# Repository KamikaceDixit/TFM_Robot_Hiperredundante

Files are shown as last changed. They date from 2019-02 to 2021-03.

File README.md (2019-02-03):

# MACH I. Un manipulador actuado por cables hiperredundante
MACH I es el resultado de un proyecto de fin de máster realizado en la Escuela Superior de Ingenieros Industriales de la UPM. El objetivo de dicho proyecto era construir un robot hiperredundante funcional, que pudiera ser utilizado en un futuro para probar nuevos algoritmos de movimiento en este tipo de robots. El resultado del proyecto es el siguiente.

<div>
<a href="../../tree/master/Renders">
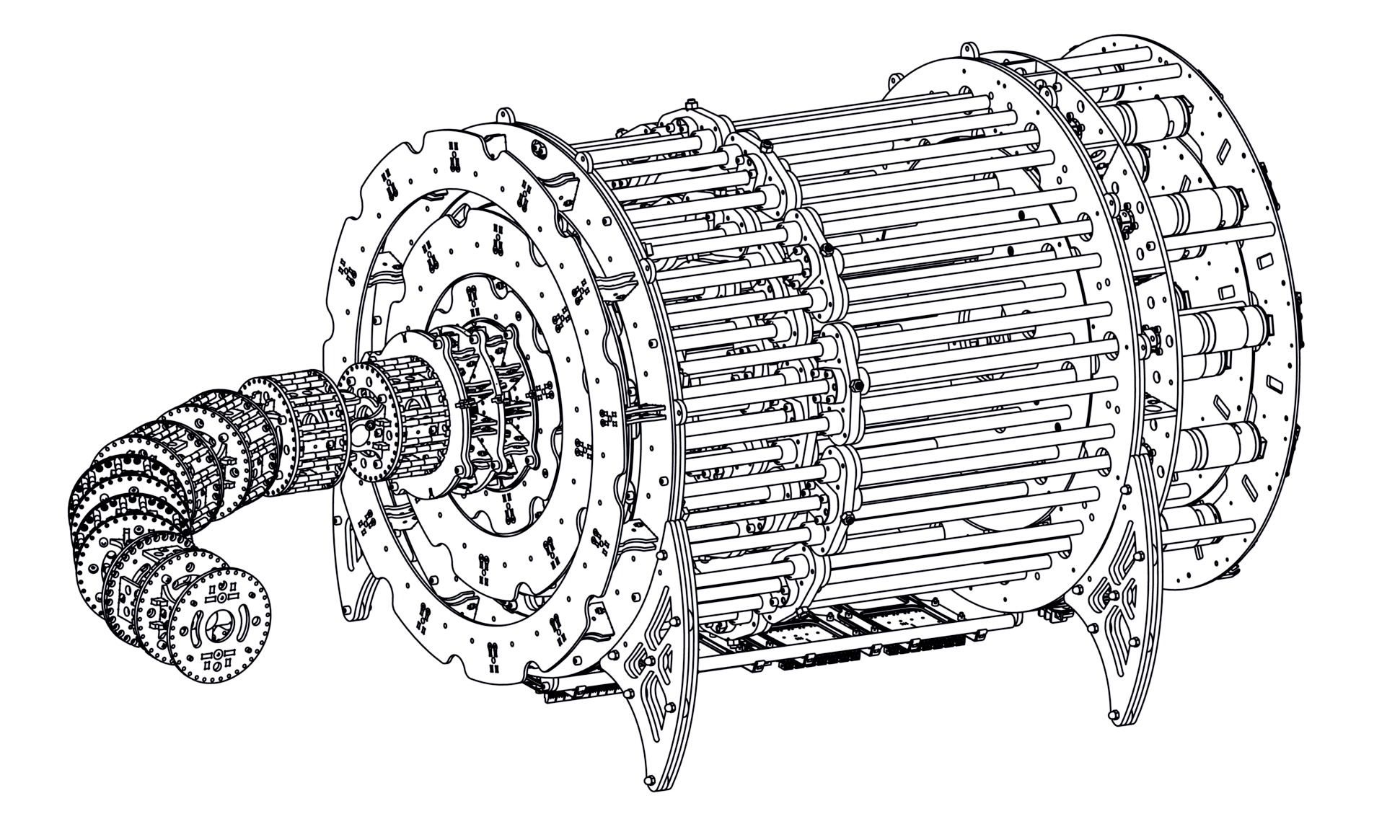
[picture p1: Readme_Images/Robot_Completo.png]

</a>
</div>

Se trata de un robot hiperredundante con 17 grados de libertad. Se compone de 7 rótulas con 2 grados de libertad cada una una, más 3 gdl extra para poder accionar una pinza o cualquier otro elemento en el extremo.
Cada rótula esta controlada con 3 cables equidistantes 120º y el rango de giro de cada una es de 33º con respecto a cualquier eje contenido en el plano paralelo a la base fija de la rótula que pase por el centro de la misma.

La concepción de MACH I se divide en 3 partes:
- Parte mecánica
- Parte electrónica y eléctrica
- Parte de programación
<hr />
En el repositorio, el proyecto esta descompuesto en varias carpetas.

### CAD y Planos
En dicha carpeta se encuentran todos los archivos CAD pertenecientes la proyecto. Estan desarrollados en CATIA V5 R21.
### Control Dinámico
Se recogen los ficheros de Matlab y diversas pruebas realizadas para caracterizar el conjunto "control+motor" para poder ajustar los diferentes parametros del control. En él se encuentran diversos archivos de Matlab y Simulink.
### PCBs
Se encuentran todos los ficheros utilizados para realizar las placas de electrónica, incluyendo esquemáticos, pcbs y librerías.
### Programas
Aquí estan desarrollados los programas integrados en cada placa y la Interfaz Hombre Máquina desarrollada en Matlab.
### Renders
Carpeta que recoge varios Renders realizados a partir del CAD.
<hr />

Adicionalmente, se recoge diverso material gráfico del proyecto en Flickr y YouTube, y puede ser consultado en los siguiente enlaces:
<div align="center">
<a href="https://www.flickr.com/photos/156143787@N03/collections/72157706450447504/">
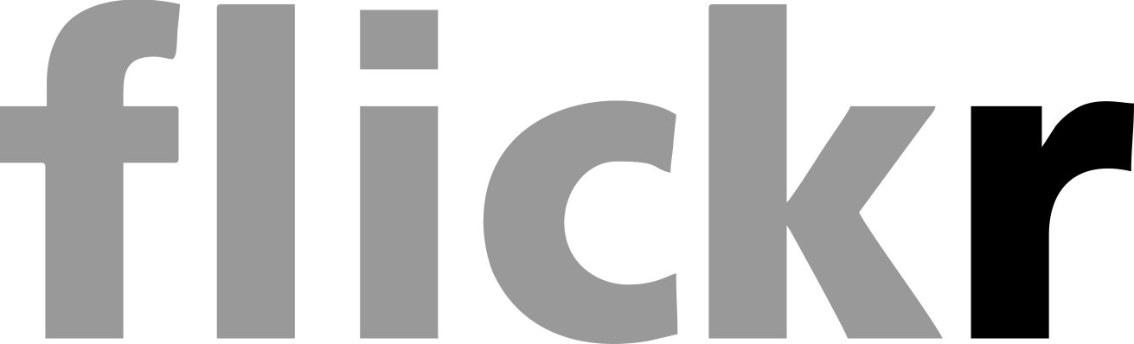
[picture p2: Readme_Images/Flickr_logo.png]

</a>
<a href="https://www.youtube.com/playlist?list=PLwVt_GYxzsi9YXO1_7UndzVlK2NOCYKW8">
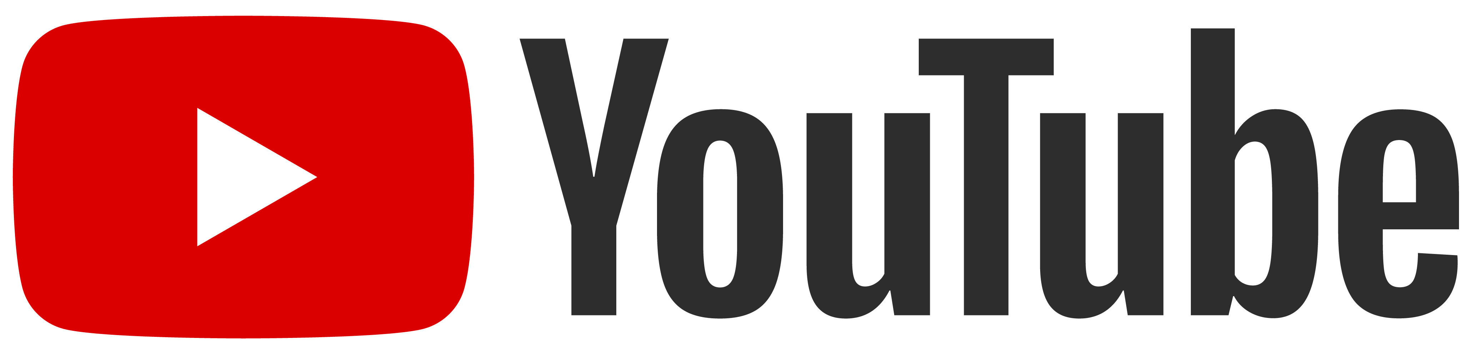
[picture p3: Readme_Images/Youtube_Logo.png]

</a>
</div>

<hr />

<a data-flickr-embed="true" data-footer="true" data-context="true"  href="https://www.flickr.com/photos/156143787@N03/46243925134/" title="Robot_3">Robot_3</a>

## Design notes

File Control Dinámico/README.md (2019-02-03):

# Control dínamico Motores
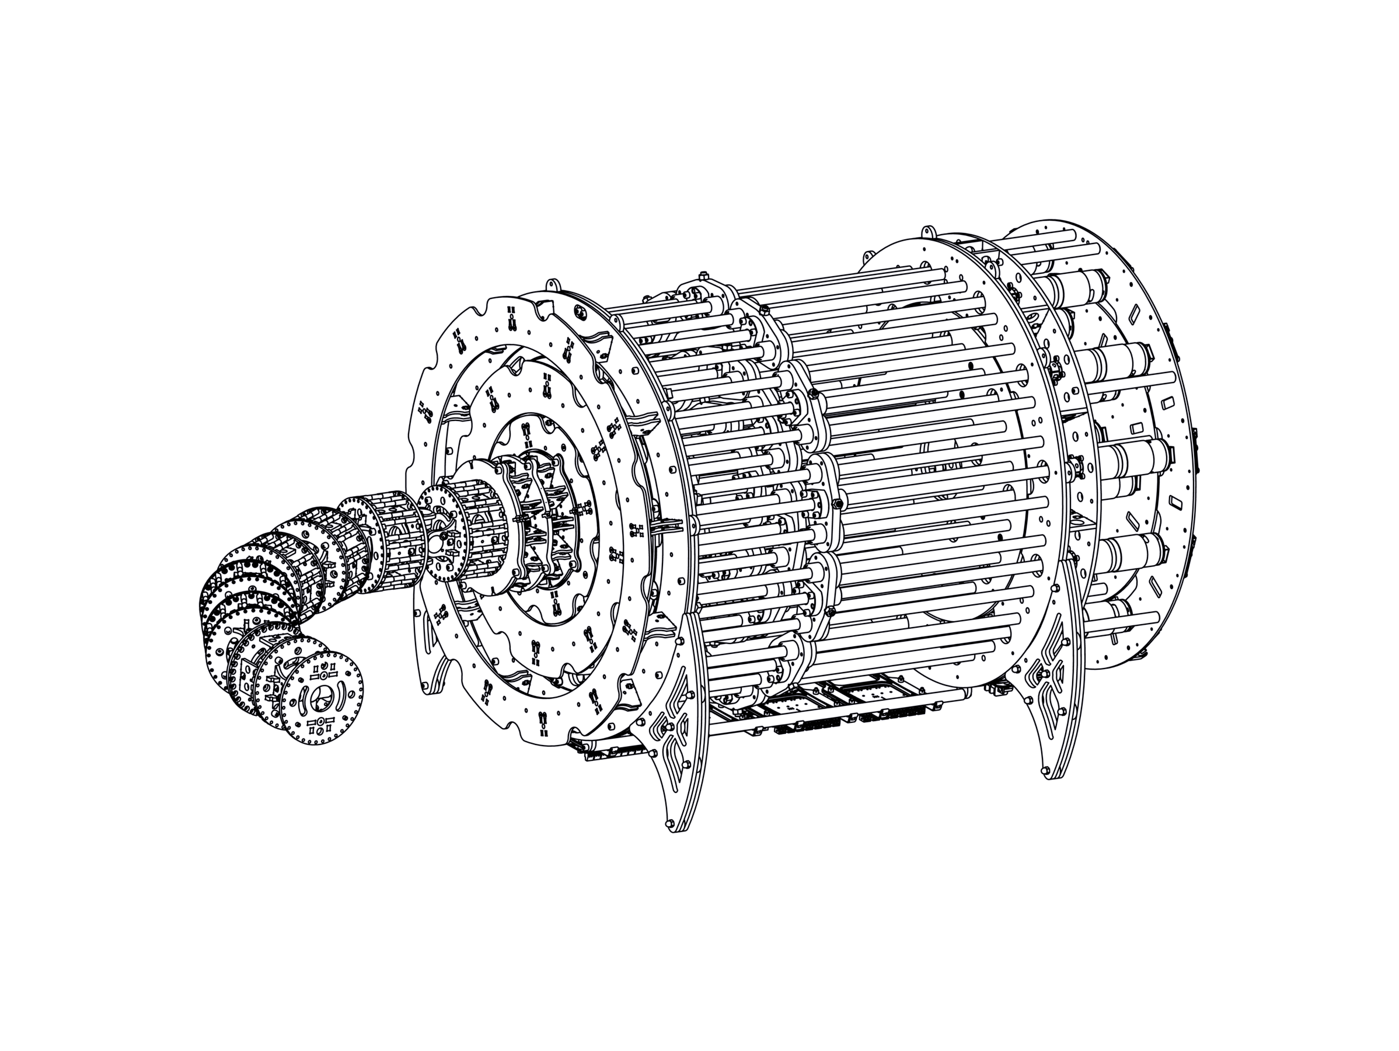
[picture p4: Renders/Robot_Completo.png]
N|Solid


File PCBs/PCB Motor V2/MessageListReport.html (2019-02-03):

Altium customize

# Message List

Date: | | 11/06/2018
Time: | | 3:35:03
Elapsed Time: | | 00:00:00

Class | Document | Source | Message | Time | Date | No.
Situs Event | Placa_Sencilla_v2.PcbDoc | Situs | Routing Started | 3:31:26 | 11/06/2018 | 1
Routing Status | Placa_Sencilla_v2.PcbDoc | Situs | Creating topology map | 3:31:26 | 11/06/2018 | 2
Situs Event | Placa_Sencilla_v2.PcbDoc | Situs | Starting Fan out to Plane | 3:31:26 | 11/06/2018 | 3
Situs Event | Placa_Sencilla_v2.PcbDoc | Situs | Completed Fan out to Plane in 0 Seconds | 3:31:26 | 11/06/2018 | 4
Situs Event | Placa_Sencilla_v2.PcbDoc | Situs | Starting Memory | 3:31:26 | 11/06/2018 | 5
Situs Event | Placa_Sencilla_v2.PcbDoc | Situs | Completed Memory in 0 Seconds | 3:31:27 | 11/06/2018 | 6
Situs Event | Placa_Sencilla_v2.PcbDoc | Situs | Starting Layer Patterns | 3:31:27 | 11/06/2018 | 7
Routing Status | Placa_Sencilla_v2.PcbDoc | Situs | 78 of 161 connections routed (48,45%) in 3 Seconds | 3:31:29 | 11/06/2018 | 8
Situs Event | Placa_Sencilla_v2.PcbDoc | Situs | Completed Layer Patterns in 3 Seconds | 3:31:30 | 11/06/2018 | 9
Situs Event | Placa_Sencilla_v2.PcbDoc | Situs | Starting Multilayer Main | 3:31:30 | 11/06/2018 | 10
Routing Status | Placa_Sencilla_v2.PcbDoc | Situs | 159 of 161 connections routed (98,76%) in 2 Minutes 58 Seconds | 3:34:24 | 11/06/2018 | 11
Situs Event | Placa_Sencilla_v2.PcbDoc | Situs | Completed Multilayer Main in 2 Minutes 54 Seconds | 3:34:25 | 11/06/2018 | 12
Situs Event | Placa_Sencilla_v2.PcbDoc | Situs | Starting Completion | 3:34:25 | 11/06/2018 | 13
Routing Status | Placa_Sencilla_v2.PcbDoc | Situs | 160 of 161 connections routed (99,38%) in 3 Minutes 7 Seconds | 3:34:33 | 11/06/2018 | 14
Situs Event | Placa_Sencilla_v2.PcbDoc | Situs | Completed Completion in 8 Seconds | 3:34:33 | 11/06/2018 | 15
Situs Event | Placa_Sencilla_v2.PcbDoc | Situs | Starting Spread | 3:34:33 | 11/06/2018 | 16
Routing Status | Placa_Sencilla_v2.PcbDoc | Situs | 160 of 161 connections routed (99,38%) in 3 Minutes 13 Seconds | 3:34:39 | 11/06/2018 | 17
Situs Event | Placa_Sencilla_v2.PcbDoc | Situs | Completed Spread in 6 Seconds | 3:34:40 | 11/06/2018 | 18
Situs Event | Placa_Sencilla_v2.PcbDoc | Situs | Starting Straighten | 3:34:40 | 11/06/2018 | 19
Routing Status | Placa_Sencilla_v2.PcbDoc | Situs | 160 of 161 connections routed (99,38%) in 3 Minutes 17 Seconds | 3:34:43 | 11/06/2018 | 20
Situs Event | Placa_Sencilla_v2.PcbDoc | Situs | Completed Straighten in 4 Seconds | 3:34:44 | 11/06/2018 | 21
Routing Status | Placa_Sencilla_v2.PcbDoc | Situs | 160 of 161 connections routed (99,38%) in 3 Minutes 18 Seconds | 3:34:44 | 11/06/2018 | 22
Situs Event | Placa_Sencilla_v2.PcbDoc | Situs | Routing finished with 0 contentions(s). Failed to complete 1 connection(s) in 3 Minutes 18 Seconds | 3:34:44 | 11/06/2018 | 23

Back to top

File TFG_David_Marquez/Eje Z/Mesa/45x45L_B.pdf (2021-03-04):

# Profile 45x45L B-Type slot 10

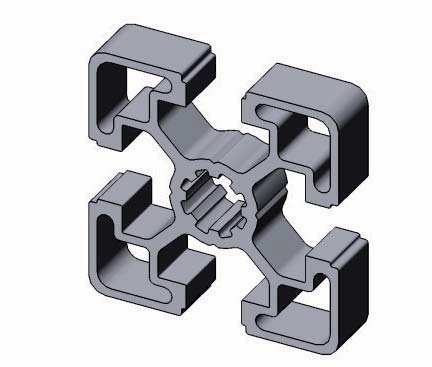
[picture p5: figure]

Profile 45x45L B-Type slot 10

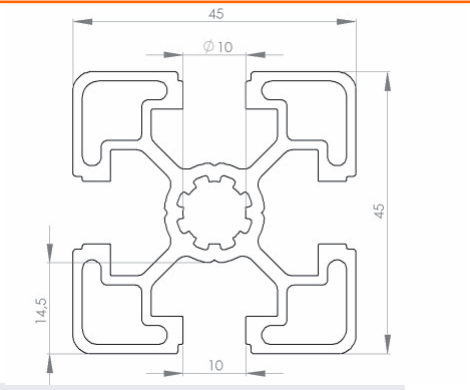
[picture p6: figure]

Slot | | 10 | mm
Mass | m | 1,50 | Kg/m
Moment of Inertia | Ix | 11,00 | cm⁴
| Iy | 11,00 | cm⁴
Section modulus | Wx | 4,80 | cm³
| Wy | 4,80 | cm³
Surface | A | 5,70 | cm²

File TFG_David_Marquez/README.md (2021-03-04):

# Control y Teleoperación de Mach I, un robot manipulador híper redundante para tareas de inspección
Trabajo de Fin de Grado de David Márquez Alcolea para la obtención del Grado en Ingeniería en Tecnologías Industriales de la ETSII - UPM.

<hr />
En el repositorio, el proyecto está descompuesto en varias carpetas.

### Eje Z
Compone los ensamblajes y piezas diseñadas para el mecanismo de movimiento lineal del eje Z del robot Mach I.
### PCB_Emergencia
Compone todos los archivos de diseño, datasheets, código y librerías de la placa electrónica para casos de emergencia diseñada para el robot.
### Unity
Se encuentran los proyectos del simulador creado en el motor gráfico Unity3D. Se debe remarcar que GitHub no permite subir archivos de más de 100mb, por lo que hay archivos críticos que no han podido subirse a este repositorio, como los modelos 3D del robot. Contactar con el creador para recibir estos archivos.

<hr />

Adicionalmente, se recoge diverso material gráfico del proyecto en Flickr y YouTube, y puede ser consultado en los siguiente enlaces:
<div align="center">
<a href="https://flic.kr/s/aHsmUDHa3X">

</a>
<a href="https://www.youtube.com/watch?v=YmS-nTq0sPs&list=PL655qwW_R3OX9st5jwc-Hn8Ow5uMBquOL">

</a>
</div>

<hr />

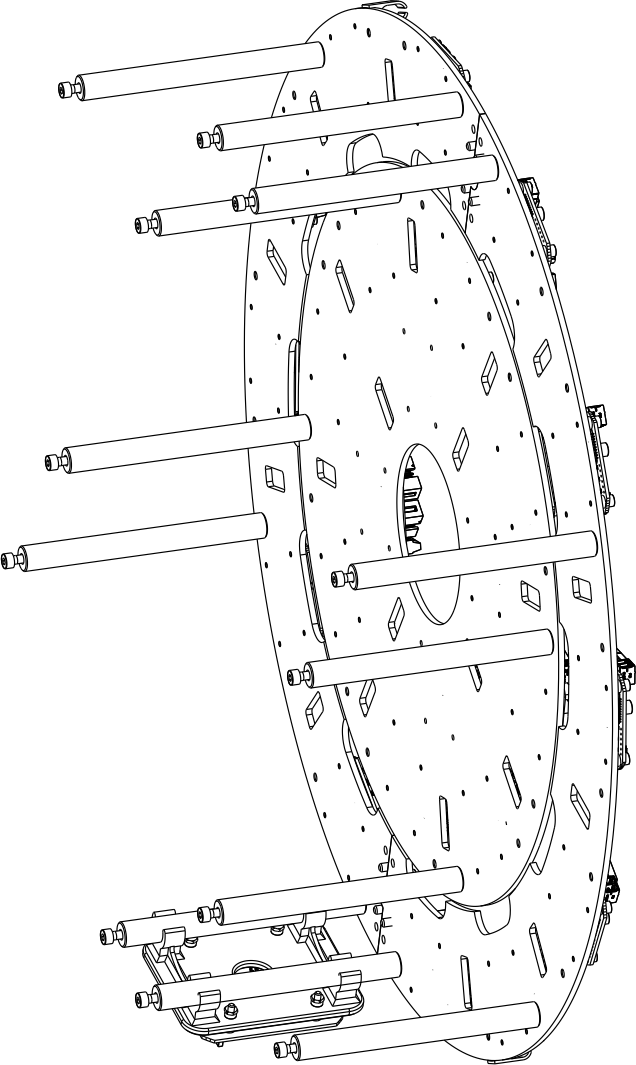
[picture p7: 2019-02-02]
Renders/Placa_Electronica.png

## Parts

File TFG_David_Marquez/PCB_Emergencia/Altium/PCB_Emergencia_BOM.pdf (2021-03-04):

Bill of Materials | Bill of Materials for PCB Emergencia
Source Data From: | BOM.BomDoc
Project: | PCB_Emergencia.PrjPcb
Variant: | 1,0
Designator | Name | LibRef | Footprint | Description | Quantity
C1, C2, C3, C4, C5, C6, C7, C8, C9, C10, C11, C12, C15, C16, C17, C18, C19, C21, C22, C23
Capacitors. | CAP0805 | 0805 | 20
C13, C14 | 47u | 47UF-50V-20% | PANASONIC_D | 2
C20 | 4.7u | 47UF-50V-20% | PANASONIC_D | 1
D1, D4, D6 | SS26FL | SS26FL | SS26FL | 3
D2 | LED Encendido | LED1206 | LED-1206 | 1
D3 | LED Parada | LED1206 | LED-1206 | 1
D5 | 13V Zener MM1Z13 | DIODE-ZENER16V | SOD-123 | 1
D7 | LED Standby | LED1206 | LED-1206 | 1
D8 | LED Carga | LED1206 | LED-1206 | 1
IC1 | TP4056 | TP4056 | *SOP-8 | 1
JP1, JP2 | JUMPER-PAD-2- NC_BY_PASTE | JUMPER-PAD-2- NC_BY_PASTE | PAD-JUMPER-2- NC_BY_PASTE_YES_SILK | 2
L1 | CDRH74 | CDRH74 | CDRH74 | 1
L2 | SMMS1360 | INDUCTOR | SMMS1360 | 1
Q1 | IRF7832TRPBF | N-MOSFET-SO8S | SO-08 | 1
R1, R2, R3, R4, R5, R6, R7, R8, R9, R10, R11, R14, R15, R16, R18, R19, R20 | Resistors. | RESISTOR0805-RES | 0805 | 17
R12 | 20K | RESISTOR0805-RES | 0805 | | 1
R13, R17 | 3296W | 3296W | 3296W | | 2
U2 | NCP1117 | V_REG_LM1117SOT223 | SOT223 | | 1
U1 | ATmega328-AU | ATmega328-AU | 32A_N | 8-bit AVR Microcontroller, 32KB Flash, 1KB EEPROM, 2KB SRAM, 32-pin TQFP, Industrial Grade (-40°C to 85°C) | 1
Y1, Y2 | 16MHz | NX3225SA-16.000MHZ-STD- CSR-1 | NDK NX3225SA | CRYSTAL 16.0000MHZ 8PF SMD | 2
E_C1, E_C2 | Header 2 | Header 2 | HDR1X2 | Header, 2-Pin | 2
P1 | IDC2X4 | IDC2X4 | IDC2X4 | Header, 4-Pin, Dual row | 1
Prog1 | Header 6 | Header 6 | HDR1X6 | Header, 6-Pin | 1
U4 | MT3608 | MT3608 | *SOT23-6 | High Efficiency 1.2MHz 2A Step Up Converter | 1
MCP2 | MCP2551T-I/SN | MCP2551T-I/SN | SOIC-SN8_N | High-Speed CAN Transceiver, 8-Pin SOIC, Industrial Temperature, Tape and Reel | 1
J1 | Conector JST | S2B-PH-K-S(LF)(SN) | *JST_S2B-PH-K-S(LF)(SN) | PH Series 2 Position 2.0 mm Through Hole Side Entry Shrouded Header | 1
U3 | LM2596S | LM2596S | LM2596S | Semiconductors and Actives | 1
MCP1 | MCP2515T-I/SO | MCP2515T-I/SO | SOIC-SO18_N | Stand-Alone CAN Controller With SPI Interface, 18-Pin SOIC, Industrial | 1
S1 | FSMSMTR | FSMSMTR | TE FSMSMTR | SWITCH TACTILE SPST-NO 0.05A 24V | 1
J2 | 20020110-D021A01LF | 20020110-D021A01LF | FCI 06-381-2PIN | TERM BLOCK HDR 2POS R/A 3.81MM | 1
| | | | | 72
Altium Limited Confidential | 29/11/2020 | Page 1

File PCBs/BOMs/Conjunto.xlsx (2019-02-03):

Bill of Materials
Source Data From: |  | Placas_PCB
Project: |  | Robot_Hiperredundante
Variant:
Creation Date: | 13/06/2018 | 1:45:41
Print Date: | 2018-07-05 | 16:44:05
Footprint | Comment | Link | Designator | Description | Quantity | A pedir | Control | Alimentacion | Fdc | Motores | 9V
0805 | 100n | https://lcsc.com/product-detail/Multilayer-Ceramic-Capacitors-MLCC-SMD-SMT_100nF-104-10-50V_C38141.html |  |  | 224 | 250 | 7 | 42 | 7 | 168
0805 | 22p | https://lcsc.com/product-detail/Multilayer-Ceramic-Capacitors-MLCC-SMD-SMT_22pF-220-5-50V_C105623.html |  |  | 137 | 200 | 2 | 10 | 5 | 120
0805 | 33n | https://lcsc.com/product-detail/Multilayer-Ceramic-Capacitors-MLCC-SMD-SMT_33nF-333-10-50V_C107150.html |  |  | 24 | 50 |  |  |  | 24
0805 | 1u | https://lcsc.com/product-detail/Multilayer-Ceramic-Capacitors-MLCC-SMD-SMT_1uF-105-5-25V_C106837.html |  |  | 24 | 40 |  |  |  | 24
0805 | 5.6K | https://lcsc.com/product-detail/Chip-Resistor-Surface-Mount_5-6KR-562-5_C102031.html |  |  | 24 | 100 |  |  |  | 24
0805 | 560 | https://lcsc.com/product-detail/Chip-Resistor-Surface-Mount_560R-5600-1_C178146.html |  |  | 57 | 100 | 3 | 4 | 2 | 48
0805 | 124 | https://lcsc.com/product-detail/Chip-Resistor-Surface-Mount-UniOhm_Uniroyal-Elec-0805W8F1240T5E_C17441.html |  |  | 28 | 50 | 1 | 2 | 1 | 24
0805 | 10K | https://lcsc.com/product-detail/Chip-Resistor-Surface-Mount_10KR-1002-1_C103904.html |  |  | 83 | 100 | 2 | 6 | 3 | 72
0805 | 200 | https://lcsc.com/product-detail/Chip-Resistor-Surface-Mount_200R-200R-1_C114567.html |  |  | 24 | 100 |  |  |  | 24
0805 | 47k | https://lcsc.com/product-detail/Chip-Resistor-Surface-Mount_47KR-473-5_C164001.html |  |  | 24 | 100 |  |  |  | 24
0805 | 20K | https://lcsc.com/product-detail/Chip-Resistor-Surface-Mount_20KR-203-5_C114233.html |  |  | 24 | 100 |  |  |  | 24
0805 | 4.7K | https://lcsc.com/product-detail/Chip-Resistor-Surface-Mount-UniOhm_Uniroyal-Elec-0805W8J0472T5E_C26022.html |  |  | 29 | 100 | 1 | 2 | 1 | 24 | 1
32A_N | ATmega328P-AU | https://lcsc.com/product-detail/ATMEL-AVR_ATMEL_ATMEGA328P-AU_ATMEGA328P-AU_C14877.html |  | 8-bit AVR Microcontroller, 32KB Flash, 1KB EEPROM, 2KB SRAM, 32-pin TQFP, Industrial Grade (-40°C to 85°C) | 27 | 32 |  | 2 | 1 | 24
FCI 06-381-2PIN | 20020110-D021A01LF | https://lcsc.com/product-detail/15EDG-Connectors_WJ15EDGRC-3-81-2P_C8387.html |  | TERM BLOCK HDR 2POS R/A 3.81MM | 52 | 60 |  | 28 |  | 24
HDR1X2 | Header 2 | https://lcsc.com/product-detail/Male-Header_2-54mm-1-40P-Straight-Headers-Pins_C2337.html |  | Header, 2-Pin | 28 | 5 | 1 | 2 | 1 | 24
HDR1X6 | Header 6 | https://lcsc.com/product-detail/Female-Header_Female-header-1-6p_C40877.html |  | Header, 6-Pin | 28 | 10 | 1 | 2 | 1 | 24
HDR2X3 | Header 3X2 | https://lcsc.com/product-detail/Male-Header_2-54mm-2-3P-Header_C65114.html |  |  | 27 | 20 |  | 2 | 1 | 24
HDR2X8_CEN | Header 8X2A | https://lcsc.com/product-detail/Male-Header_Headers-Pins2-8P-pitch2-54mm-Straight-line_C68234.html |  | Header, 8-Pin, Dual row | 2 | 10 |  |  | 2
IDC2X4 | IDC2X4 | https://lcsc.com/product-detail/Header-Connectors_2-54mm-2-4-Straight-IDC-Box_C9135.html |  | Conector IDC 2x4 | 62 | 70 | 4 | 4 | 2 | 48 | 4
LED-1206 | 1206 LED | https://lcsc.com/product-detail/Light-Emitting-Diodes-LED_LEDBright-red-light-1206_C49018.html |  | Rojo | 82 | 100 | 3 | 4 | 2 | 72 | 1
14x2 |  | https://lcsc.com/product-detail/Female-Header_DS1023-2-14SF11_C132128.html |  |  |  | 2
5x2 |  | https://lcsc.com/product-detail/Female-Header_Shenzhen-Cancome-Female-header-2-5P-2-54mm-Straight-line_C124423.html |  |  |  | 5
20x2 |  | https://lcsc.com/product-detail/Female-Header_2-54mm-2-20PFemale-header_C50982.html |  |  |  | 2
1x2 |  | https://lcsc.com/product-detail/Female-Header_2-54-1-2PFemale_C49661.html |  |  |  | 20
NDK NX3225SA | 16MHz | https://lcsc.com/product-detail/SMD-Crystals_YSX321SL-16MHZ-9PF-10PPM-40-85_C13738.html |  | CRYSTAL 16.0000MHZ 8PF SMD | 55 | 60 | 1 | 4 | 2 | 48
PANASONIC_D | 100u | https://lcsc.com/product-detail/Aluminum-Electrolytic-Capacitors-SMD_100uF-35V_C129419.html |  |  | 24 | 30 |  |  |  | 24
PANASONIC_D | 47u | https://lcsc.com/product-detail/Aluminum-Electrolytic-Capacitors-SMD_47uF-20-35V_C129415.html |  |  | 56 | 70 | 2 | 4 | 2 | 48
POWERDI-123 | SBR3U40P1-7 | https://lcsc.com/product-detail/Diodes-General-Purpose_DIODES_SBR3U40P1-7_SBR3U40P1-7_C97127.html |  |  | 96 | 120 |  |  |  | 96
R2512 | 0.012 2W | https://lcsc.com/product-detail/Metal-Alloy-Resistors_0-012R-1-2W-alloy_C76243.html |  |  | 28 | 40 |  | 28
SOT223 | NCP1117 | https://lcsc.com/product-detail/Low-Dropout-Regulators-LDO_ON_NCP1117ST50T3G_NCP1117ST50T3G_C17314.html |  |  | 28 | 35 | 1 | 2 | 1 | 24
SO-08 | IRF7832TRPBF | https://lcsc.com/product-detail/MOSFET_IR_IRF7832TRPBF_IRF7832TRPBF_C3002.html |  |  | 24 | 30 |  |  |  | 24
SOD-123 | SOD123-1A | https://lcsc.com/product-detail/Diodes-General-Purpose_1N4004W_C162734.html |  |  | 28 | 50 | 1 | 2 | 1 | 24
SOD-123 | 13V Zener MM1Z13 | https://lcsc.com/product-detail/Zener-Diodes_MM1Z13_C107588.html |  |  | 24 | 40 |  |  |  | 24
SOIC-SN8_N | MCP2551T-I/SN | https://lcsc.com/product-detail/CAN_MICROCHIP_MCP2551-I-SN_MCP2551-I-SN_C7376.html |  | High-Speed CAN Transceiver, 8-Pin SOIC, Industrial Temperature, Tape and Reel | 28 | 32 | 1 | 2 | 1 | 24
SOIC-SO18_N | MCP2515T-E/SO | https://lcsc.com/product-detail/CAN_MICROCHIP_MCP2515T-I-SO_MCP2515T-I-SO_C153782.html |  | Stand-Alone CAN Controller With SPI Interface, 18-Pin SOIC, Extended Temperature, Tape and Reel | 28 | 32 | 1 | 2 | 1 | 24
TE FSMSMTR | FSMSMTR | https://lcsc.com/product-detail/Tactile-Switches_K2-1101ST-A4SW-01black_C136740.html |  | SWITCH TACTILE SPST-NO 0.05A 24V | 27 | 40 |  | 2 | 1 | 24
WJ45C-B-2P | WJ45C-B-2P | https://lcsc.com/product-detail/Terminal-Blocks_WJ45C-B-2P_C8397.html |  |  | 3 | 15 |  | 2 |  |  | 1 | 7
Conector Macho 3,81mm |  | https://lcsc.com/product-detail/15EDG-Connectors_WJ15EDGK-3-81-2P_C8466.html |  |  | 0 | 60
Conector Macho IDC |  | https://lcsc.com/product-detail/Header-Connectors_2-54mm-2-4P-Crimping-terminals_C21851.html |  |  | 0 | 50
Conector DC 9V |  | https://lcsc.com/product-detail/DC-Connectors_high-quality-DC-005-Inner-core2-0mm_C84007.html |  |  | 2 | 5 |  |  |  |  | 2
Jumpers |  | https://lcsc.com/product-detail/Shunts-Jumpers_2-54mm-Short-hood_C5305.html |  |  |  | 50
Schotty Diode | STPS4030CT | https://lcsc.com/product-detail/Others_STMicroelectronics_STPS4030CT_STPS4030CT_C160205.html |  |  |  | 5
0805 | 0 | - |  |  | 54 | - |  | 4 | 2 | 48
Mega2560Pro_Layout | RobotDyn Mega 2560 Pro | - |  | RobotDyn Mega 2560 Pro | 1 | 1 | 1
SOIC127P1420X340-21N | MC33887 | http://es.farnell.com/nxp/mc33887apvw/motor-control-5a-h-brdg-10khz/dp/2308043?st=MC33887 |  |  | 24 | 30 |  |  |  | 24
SOP50P310X90-8N | TXB0102 | http://www.ti.com/product/TXB0102/samplebuy |  | 2-Bit Bidirectional Voltage-Level Translator with Auto Direction Sensing and +/-15-kV ESD Protect | 1 | TI | 1
SO08 | INA219 | http://www.ti.com/product/INA219/samplebuy |  |  | 28 | TI |  | 28
SSOP-24 | 4067 | http://www.ti.com/product/CD74HC4067/samplebuy |  | MUX-74HC4067 | 2 | TI |  |  | 2
TE 282834-3 | 282834-3 | https://es.aliexpress.com/store/product/50-pcs-Universal-2-54-mm-Pitch-2-Pin-3-4-5-6-7-8-9/1264152_32809307718.html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 |  | TERM BLOCK 3POS SIDE ENT 2.54MM | 30 | 35 |  |  | 30
TE 282834-8 | 282834-8 | https://es.aliexpress.com/store/product/50-pcs-Universal-2-54-mm-Pitch-2-Pin-3-4-5-6-7-8-9/1264152_32809307718.html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 |  | TERM BLOCK 8POS SIDE ENT 2.54MM | 26 | 35 | 2 |  |  | 24
Cable Plano IDC |  | https://www.tme.eu/en/details/ds1057-08a282r/ribbon-cables-single-color/connfly/ds1057-08a282r-305/ |  |  |  | 30,5m
Cable 2 Hilos Alimentacion Motor |  | https://www.tme.eu/en/details/sc-cca2x0.75-rb100/speaker-cables/goobay/15022/ |  |  |  | 100m
Cable 2 Hilos Alimentacion PCB 2,5 |  | https://www.tme.eu/en/details/sc-cu2x2.50-rb010/speaker-cables/goobay/15099/ |  |  |  | 20m
Pasacables 2,5 |  | https://www.tme.eu/es/details/odz-10l/pasacables/ |  |  |  | 5
CAM Switch |  | https://www.tme.eu/es/details/gx1610u25/conmutadores-de-levas/lovato-electric/ |  |  |  | 1
Conector Horquilla M4 2,5mm2 |  | https://www.tme.eu/es/details/bm00220/conectores-aislados/bm-group/bm-00220/ |  |  |  | 50
Conector 6,3x0,8 2,5mm2 |  | https://www.tme.eu/es/details/bm00291/conectores-aislados/bm-group/bm-00291/ |  |  |  | 50
Conector Panel Output |  | https://www.tme.eu/en/details/4798.9000/iec-60320-connectors/schurter/ |  |  |  | 4
Conector Cable Output |  | https://www.tme.eu/en/details/px0599/iec-60320-connectors/bulgin/ |  |  |  | 4
Bridas |  | https://www.tme.eu/es/details/cv-200aw/bridas-sujetacables/kss-wiring/cvr200aw/ |  |  |  | 200
Portabridas Autoadhesivo |  | https://www.tme.eu/es/details/hc-100-s4/sujecciones-para-eslingas/kss-wiring/ |  |  |  | 50
Portabridas Tornillo |  | https://www.tme.eu/es/details/hc-1/sujecciones-para-eslingas/kss-wiring/ |  |  |  | 100
Cable Fuente |  | https://www.tme.eu/en/details/sn311-3_07_1.8b/universal-and-computer-power-cords/lian-dung/ |  |  |  | 2
Fuente Alimentacion 9V |  | https://www.tme.eu/en/details/gst60a09-p1j/desktop-power-supplies/mean-well/ |  |  |  | 1
Pulsador Emergencia |  | https://www.tme.eu/en/details/las0-k-11tsa_rip65/panel-mount-switches-standard-22mm/onpow/las0-k-11tsarip65/ |  |  |  | 1
Conector Alimentacion Panel |  | https://www.tme.eu/es/details/iec-a-1/conectores-iec-60309/adam-tech/ |  |  |  | 2
Armario Fuentes |  | https://www.tme.eu/es/details/epn-2755-00/carcasas-de-pared/elektro-plast-nasielsk/2755-00/ |  |  |  | 1
Magneto 10A |  | https://www.tme.eu/es/details/a9f03210/disyuntores/schneider-electric/ |  |  |  | 1
Carril DIN |  | https://www.tme.eu/es/details/ekv-12/carcasas-otros-accesorios/fibox/ekv-12/ |  |  |  | 1
 |  |  |  |  | 1429
Approved |  | Notes
 |  |  |  |  |  |  | 32 | 158 | 38 | 1320 | 9

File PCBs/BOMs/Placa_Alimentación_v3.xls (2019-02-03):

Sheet: BOM Report
Bill of Materials |  |  | Bill of Materials For PCB Document [Placa_Alimentación_v3.PcbDoc]
Source Data From: |  | Placa_Alimentación_v3.PcbDoc
Project: |  | Placa_Alimentación.PrjPCB
Variant: |  | None
Creation Date: | 13/06/2018 | 1:40:26
Print Date: | 2018-06-13 | 2:06:06
Footprint | Comment | #Column Name Error:LibRef | Designator | Description | Quantity
LED-1206 | 1206 LED |  | 5V, L1 |  | 2 | 4
0805 | 100n |  | C1, C4, C5, C6, C7, C11, C14_S1, C14_S2, C14_S3, C14_S4, C14_S5, C14_S6, C14_S7, C14_S8, C14_S9, C14_S10, C14_S11, C14_S12, C14_S13, C14_S14, C15 |  | 21 | 42
PANASONIC_D | 47u |  | C2, C10 |  | 2 | 4
0805 | 22p |  | C3, C8, C9, C12, C13 |  | 5 | 10
SOD-123 | SOD123-1A |  | D1 |  | 1 | 2
HDR1X2 | Header 2 |  | E_C1 | Header, 2-Pin | 1 | 2
PAD-JUMPER-2-NO_YES_SILK | JUMPER-PAD-2-NOYES_SILK |  | GND1, GND2, SCL1, SCL2, SDA1, SDA2 |  | 6
SO08 | INA219 |  | IC1_S1, IC1_S2, IC1_S3, IC1_S4, IC1_S5, IC1_S6, IC1_S7, IC1_S8, IC1_S9, IC1_S10, IC1_S11, IC1_S12, IC1_S13, IC1_S14 |  | 14 | 28
HDR2X3 | Header 3X2 |  | ISCP1 | Header, 3-Pin, Dual row | 1 | 2
PAD-JUMPER-3-NO_YES_SILK | JUMPER-PAD-3-NOYES_SILK |  | JP1_S1, JP1_S2, JP1_S3, JP1_S4, JP1_S5, JP1_S6, JP1_S7, JP1_S8, JP1_S9, JP1_S10, JP1_S11, JP1_S12, JP1_S13, JP1_S14, JP2_S1, JP2_S2, JP2_S3, JP2_S4, JP2_S5, JP2_S6, JP2_S7, JP2_S8, JP2_S9, JP2_S10, JP2_S11, JP2_S12, JP2_S13, JP2_S14, JP3_S1, JP3_S2, JP3_S3, JP3_S4, JP3_S5, JP3_S6, JP3_S7, JP3_S8, JP3_S9, JP3_S10, JP3_S11, JP3_S12, JP3_S13, JP3_S14, JP4_S1, JP4_S2, JP4_S3, JP4_S4, JP4_S5, JP4_S6, JP4_S7, JP4_S8, JP4_S9, JP4_S10, JP4_S11, JP4_S12, JP4_S13, JP4_S14 |  | 56
SOIC-SN8_N | MCP2551T-I/SN |  | MCP1 | High-Speed CAN Transceiver, 8-Pin SOIC, Industrial Temperature, Tape and Reel | 1 | 2
SOIC-SO18_N | MCP2515T-E/SO |  | MCP2 | Stand-Alone CAN Controller With SPI Interface, 18-Pin SOIC, Extended Temperature, Tape and Reel | 1 | 2
FCI 06-381-2PIN | 20020110-D021A01LF |  | M_C1, M_C2, M_C3, M_C4, M_C5, M_C6, M_C7, M_C8, M_C9, M_C10, M_C11, M_C12, M_C13, M_C14 | TERM BLOCK HDR 2POS R/A 3.81MM | 14 | 28
IDC2X4 | IDC2X4 |  | P1, P2 | Header, 4-Pin, Dual row | 2 | 4
HDR1X6 | Header 6 |  | Prog1 | Header, 6-Pin | 1 | 2
0805 | 10K |  | R1, R3, R7 |  | 3 | 6
0805 | 560 |  | R2, R8 |  | 2 | 4
0805 | 0 |  | R4, R5 |  | 2 | 4
0805 | 124 |  | R6 |  | 1 | 2
0805 | 4.7K |  | R9 |  | 1 | 2
R2512 | 0.012 2W |  | R10_S1, R10_S2, R10_S3, R10_S4, R10_S5, R10_S6, R10_S7, R10_S8, R10_S9, R10_S10, R10_S11, R10_S12, R10_S13, R10_S14 |  | 14 | 28
TE FSMSMTR | FSMSMTR |  | S1 | SWITCH TACTILE SPST-NO 0.05A 24V | 1 | 2
32A_N | ATmega328P-AU |  | U1 | 8-bit AVR Microcontroller, 32KB Flash, 1KB EEPROM, 2KB SRAM, 32-pin TQFP, Industrial Grade (-40°C to 85°C) | 1 | 2
SOT223 | NCP1117 |  | U2 |  | 1 | 2
WJ45C-B-2P | WJ45C-B-2P |  | WJ45C-B-2P |  | 1 | 2
NDK NX3225SA | 16MHz |  | Y1, Y2 | CRYSTAL 16.0000MHZ 8PF SMD | 2 | 4
 |  |  |  |  | 157 | 190
Approved |  | Notes

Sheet: Project Information
Project Full Path | X:\Dropbox\Universidad\Máster\TFM\1. PCBs\PCB Alimentacion\Placa_Alimentación.PrjPCB
Project Filename | Placa_Alimentación.PrjPCB
Variant Name | None
Data-Source Filename | Placa_Alimentación_v3.PcbDoc
Data-Source Full Path | X:\Dropbox\Universidad\Máster\TFM\1. PCBs\PCB Alimentacion\Placa_Alimentación_v3.PcbDoc
Title | Bill of Materials For PCB Document [Placa_Alimentación_v3.PcbDoc]
Total Quantity | 157
Report Time | 1:40:26
Report Date | 13/06/2018
Report Date & Tine | 13/06/2018 1:40:26
Output Name | Bill of Materials
Output Type | BOM_PartType
Output Generator Name | BOM
Output Generator Description | Bill of Materials

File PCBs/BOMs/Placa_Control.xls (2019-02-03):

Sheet: BOM Report
Bill of Materials |  |  | Bill of Materials For PCB Document [Placa_Control.PcbDoc]
Source Data From: |  | Placa_Control.PcbDoc
Project: |  | Placa_Control.PrjPCB
Variant: |  | None
Creation Date: | 13/06/2018 | 1:45:41
Print Date: | 2018-06-13 | 1:45:45
Footprint | Comment | #Column Name Error:LibRef | Designator | Description | Quantity
HDR1X6 | Header 6 |  | BT1 | Header, 6-Pin | 1
0805 | 100n |  | C1, C2, C3, C4, C5, C6, C9 |  | 7
PANASONIC_D | 47u |  | C7, C8 |  | 2
0805 | 22p |  | C10, C11 |  | 2
SOD-123 | SOD123-1A |  | D1 |  | 1
HDR1X2 | Header 2 |  | E_C1 | Header, 2-Pin | 1
TE 282834-8 | 282834-8 |  | I/O1, I/O2 | TERM BLOCK 8POS SIDE ENT 2.54MM | 2
IDC2X4 | IDC2X4 |  | I/O_B1, I/O_B2, P1, P2 | Header, 4-Pin, Dual row | 4
LED-1206 | 1206 LED |  | L1, L2, L3 |  | 3
SOIC-SN8_N | MCP2551T-I/SN |  | MCP1 | High-Speed CAN Transceiver, 8-Pin SOIC, Industrial Temperature, Tape and Reel | 1
SOIC-SO18_N | MCP2515T-E/SO |  | MCP2 | Stand-Alone CAN Controller With SPI Interface, 18-Pin SOIC, Extended Temperature, Tape and Reel | 1
0805 | 560 |  | R1, R2, R3 |  | 3
0805 | 124 |  | R4 |  | 1
0805 | 10K |  | R5, R7 |  | 2
0805 | 4.7K |  | R6 |  | 1
Mega2560Pro_Layout | RobotDyn Mega 2560 Pro |  | U1 | RobotDyn Mega 2560 Pro | 1
SOP50P310X90-8N | TXB0102 |  | U2 | 2-Bit Bidirectional Voltage-Level Translator with Auto Direction Sensing and +/-15-kV ESD Protect | 1
SOT223 | NCP1117 |  | U3 |  | 1
NDK NX3225SA | 16MHz |  | Y1 | CRYSTAL 16.0000MHZ 8PF SMD | 1
 |  |  |  |  | 36
Approved |  | Notes

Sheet: Project Information
Project Full Path | X:\Dropbox\Universidad\Máster\TFM\1. PCBs\PCB Control\Placa_Control.PrjPCB
Project Filename | Placa_Control.PrjPCB
Variant Name | None
Data-Source Filename | Placa_Control.PcbDoc
Data-Source Full Path | X:\Dropbox\Universidad\Máster\TFM\1. PCBs\PCB Control\Placa_Control.PcbDoc
Title | Bill of Materials For PCB Document [Placa_Control.PcbDoc]
Total Quantity | 36
Report Time | 1:45:41
Report Date | 13/06/2018
Report Date & Tine | 13/06/2018 1:45:41
Output Name | Bill of Materials
Output Type | BOM_PartType
Output Generator Name | BOM
Output Generator Description | Bill of Materials

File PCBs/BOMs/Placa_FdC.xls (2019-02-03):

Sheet: BOM Report
Bill of Materials |  |  | Bill of Materials For PCB Document [Placa_FdC.PcbDoc]
Source Data From: |  | Placa_FdC.PcbDoc
Project: |  | Placa_FdC.PrjPCB
Variant: |  | None
Creation Date: | 13/06/2018 | 1:47:13
Print Date: | 2018-06-13 | 1:47:18
Footprint | Comment | #Column Name Error:LibRef | Designator | Description | Quantity
LED-1206 | 1206 LED |  | 5V, L1 |  | 2
0805 | 100n |  | C1, C4, C5, C6, C7, C12, C13 |  | 7
PANASONIC_D | 47u |  | C2, C17 |  | 2
0805 | 22p |  | C3, C8, C9, C10, C11 |  | 5
SOD-123 | SOD123-1A |  | D5 |  | 1
HDR1X2 | Header 2 |  | E_C | Header, 2-Pin | 1
HDR2X3 | Header 3X2 |  | ISCP | Header, 3-Pin, Dual row | 1
TE 282834-3 | 282834-3 |  | J_C1, J_C2, J_C3, J_C4, J_C5, J_C6, J_C7, J_C8, J_C9, J_C10, J_C11, J_C12, J_C13, J_C14, J_C15, J_C16, J_C17, J_C18, J_C19, J_C20, J_C21, J_C22, J_C23, J_C24, J_C25, J_C26, J_C27, J_C28, J_C29, J_C30 | TERM BLOCK 3POS SIDE ENT 2.54MM | 30
SOIC-SN8_N | MCP2551T-I/SN |  | MCP1 | High-Speed CAN Transceiver, 8-Pin SOIC, Industrial Temperature, Tape and Reel | 1
SOIC-SO18_N | MCP2515T-E/SO |  | MCP2 | Stand-Alone CAN Controller With SPI Interface, 18-Pin SOIC, Extended Temperature, Tape and Reel | 1
IDC2X4 | IDC2X4 |  | P1, P2 | Header, 4-Pin, Dual row | 2
HDR2X8_CEN | Header 8X2A |  | P3, P4 | Header, 8-Pin, Dual row | 2
HDR1X6 | Header 6 |  | Prog | Header, 6-Pin | 1
0805 | 10K |  | R1, R4, R10 |  | 3
0805 | 560 |  | R2, R8 |  | 2
0805 | 0 |  | R5, R6 |  | 2
0805 | 124 |  | R7 |  | 1
0805 | 4.7K |  | R11 |  | 1
TE FSMSMTR | FSMSMTR |  | S1 | SWITCH TACTILE SPST-NO 0.05A 24V | 1
32A_N | ATmega328P-AU |  | U1 | 8-bit AVR Microcontroller, 32KB Flash, 1KB EEPROM, 2KB SRAM, 32-pin TQFP, Industrial Grade (-40°C to 85°C) | 1
SOT223 | NCP1117 |  | U2 |  | 1
SSOP-24 | 4067 |  | U3, U4 | MUX-74HC4067 | 2
NDK NX3225SA | 16MHz |  | Y1, Y2 | CRYSTAL 16.0000MHZ 8PF SMD | 2
 |  |  |  |  | 72
Approved |  | Notes

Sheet: Project Information
Project Full Path | X:\Dropbox\Universidad\Máster\TFM\1. PCBs\PCB FdC\Placa_FdC.PrjPCB
Project Filename | Placa_FdC.PrjPCB
Variant Name | None
Data-Source Filename | Placa_FdC.PcbDoc
Data-Source Full Path | X:\Dropbox\Universidad\Máster\TFM\1. PCBs\PCB FdC\Placa_FdC.PcbDoc
Title | Bill of Materials For PCB Document [Placa_FdC.PcbDoc]
Total Quantity | 72
Report Time | 1:47:13
Report Date | 13/06/2018
Report Date & Tine | 13/06/2018 1:47:13
Output Name | Bill of Materials
Output Type | BOM_PartType
Output Generator Name | BOM
Output Generator Description | Bill of Materials

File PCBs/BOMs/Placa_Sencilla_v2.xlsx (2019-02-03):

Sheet: BOM Report
Bill of Materials |  |  | Bill of Materials For PCB Document [Placa_Sencilla_v2.PcbDoc]
Source Data From: |  | Placa_Sencilla_v2.PcbDoc
Project: |  | Placa_Motores_v2.PrjPCB
Variant: |  | None
Creation Date: | 13/06/2018 | 1:46:23
Print Date: | 2018-07-18 | 2:41:58
Footprint | Comment | #Column Name Error:LibRef | Designator | Description | Quantity
0805 | 100n |  | C1, C4, C5, C6, C7, C12, C13 |  | 7 | 168
0805 | 22p |  | C3, C8, C9, C10, C11 |  | 5 | 120
0805 | 33n |  | C15 |  | 1 | 24
0805 | 1u |  | C16 |  | 1 | 24
0805 | 10K |  | R1, R4, R10 |  | 3 | 72
0805 | 560 |  | R2, R8 |  | 2 | 48
0805 | 5.6K |  | R3 |  | 1 | 24
0805 | 0 |  | R5, R6 |  | 2 | 48
0805 | 124 |  | R7 |  | 1 | 24
0805 | 200 |  | R9 |  | 1 | 24
0805 | 4.7K |  | R11 |  | 1 | 24
0805 | 47k |  | R12 |  | 1 | 24
0805 | 20K |  | R13 |  | 1 | 24
32A_N | ATmega328P-AU |  | U1 | 8-bit AVR Microcontroller, 32KB Flash, 1KB EEPROM, 2KB SRAM, 32-pin TQFP, Industrial Grade (-40°C to 85°C) | 1 | 24
FCI 06-381-2PIN | 20020110-D021A01LF |  | POWER | TERM BLOCK HDR 2POS R/A 3.81MM | 1 | 24
HDR1X2 | Header 2 |  | E_C | Header, 2-Pin | 1 | 24
HDR1X6 | Header 6 |  | Prog | Header, 6-Pin | 1 | 24
HDR2X3 | Header 3X2 |  | ISCP | Header, 3-Pin, Dual row | 1 | 24
IDC2X4 | IDC2X4 |  | P1, P2 | Header, 4-Pin, Dual row | 2 | 48
LED-1206 | 1206 LED |  | 5V, 24V, L1 |  | 3 | 72
NDK NX3225SA | 16MHz |  | Y1, Y2 | CRYSTAL 16.0000MHZ 8PF SMD | 2 | 48
PAD-JUMPER-2-NC_BY_PASTE_YES_SILK | JUMPER-PAD-2-NC_BY_PASTE |  | JP? |  | 1
PANASONIC_D | 47u |  | C2, C17 |  | 2 | 48
PANASONIC_D | 100u |  | C14 |  | 1 | 24
POWERDI-123 | SBR3U40P1-7 |  | D1, D2, D3, D4 |  | 4 | 96
SO-08 | IRF7832TRPBF |  | Q1 |  | 1 | 24
SOD-123 | SOD123-1A |  | D5 |  | 1 | 24
SOD-123 | 13V Zener MM1Z13 |  | D6 |  | 1 | 24
SOIC127P1420X340-21N | MC33887 |  | MC1 | Motor / Motion / Ignition Controllers & Drivers 5.0 A H-BRIDGE | 1 | 24
SOIC-SN8_N | MCP2551T-I/SN |  | MCP1 | High-Speed CAN Transceiver, 8-Pin SOIC, Industrial Temperature, Tape and Reel | 1 | 24
SOIC-SO18_N | MCP2515T-E/SO |  | MCP2 | Stand-Alone CAN Controller With SPI Interface, 18-Pin SOIC, Extended Temperature, Tape and Reel | 1 | 24
SOT223 | NCP1117 |  | U2 |  | 1 | 24
TE 282834-8 | 282834-8 |  | I/O | TERM BLOCK 8POS SIDE ENT 2.54MM | 1 | 24
TE FSMSMTR | FSMSMTR |  | S1 | SWITCH TACTILE SPST-NO 0.05A 24V | 1 | 24
 |  |  |  |  | 56 | 1320
Approved |  | Notes

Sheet: Project Information
Project Full Path | X:\Dropbox\Universidad\Máster\TFM\1. PCBs\PCB Motor V2\Placa_Motores_v2.PrjPCB
Project Filename | Placa_Motores_v2.PrjPCB
Variant Name | None
Data-Source Filename | Placa_Sencilla_v2.PcbDoc
Data-Source Full Path | X:\Dropbox\Universidad\Máster\TFM\1. PCBs\PCB Motor V2\Placa_Sencilla_v2.PcbDoc
Title | Bill of Materials For PCB Document [Placa_Sencilla_v2.PcbDoc]
Total Quantity | 56
Report Time | 1:46:23
Report Date | 13/06/2018
Report Date & Tine | 13/06/2018 1:46:23
Output Name | Bill of Materials
Output Type | BOM_PartType
Output Generator Name | BOM
Output Generator Description | Bill of Materials

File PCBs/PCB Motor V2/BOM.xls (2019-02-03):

Comment | Description | Designator | Footprint | LibRef | Quantity
1206 LED |  | 5V, 24V, L1, L2 | LED-1206 | LED1206 | 4
100n |  | C1, C4, C5, C6, C7, C12, C13 | 0805 | CAP0805 | 7
47uF |  | C2, C14 | PANASONIC_D | 47UF-50V-20%(ELECT) | 2
22p |  | C3, C8, C9, C10, C11 | 0805 | CAP0805 | 5
33n |  | C15 | 0805 | CAP0805 | 1
Header 2 | Header, 2-Pin | CS_J | HDR1X2 | Header 2 | 1
Header 3 | Header, 3-Pin | END_CAN | HDR1X3 | Header 3 | 1
282834-2 | TERM BLOCK 2POS SIDE ENT 2.54MM | IN | TE 282834-2 | 282834-2 | 1
Header 3X2 | Header, 3-Pin, Dual row | ISCP | HDR2X3 | Header 3X2 | 1
MC33886PVW | Motor / Motion / Ignition Controllers & Drivers 5.0 A H-BRIDGE | MC1 | SOIC127P1420X340-21N | MC33886PVW | 1
MCP2551T-I/SN | High-Speed CAN Transceiver, 8-Pin SOIC, Industrial Temperature, Tape and Reel | MCP1 | SOIC-SN8_N | MCP2551T-I/SN | 1
MCP2515T-E/SO | Stand-Alone CAN Controller With SPI Interface, 18-Pin SOIC, Extended Temperature, Tape and Reel | MCP2 | SOIC-SO18_N | MCP2515T-E/SO | 1
282834-6 | TERM BLOCK 6POS SIDE ENT 2.54MM | MOTOR | TE 282834-6 | 282834-6 | 1
Header 4X2 | Header, 4-Pin, Dual row | P1, P2 | HDR2X4 | Header 4X2 | 2
Alimentacion 24V | TERM BLOCK HDR 2POS R/A 3.81MM | POWER | FCI 06-381-2PIN | 20020110-D021A01LF | 1
Header 6 | Header, 6-Pin | Prog1 | HDR1X6 | Header 6 | 1
10K |  | R1, R4, R10 | 0805 | RESISTOR0805-RES | 3
500 |  | R2, R8, R9 | 0805 | RESISTOR0805-RES | 3
5.2K |  | R3 | 0805 | RESISTOR0805-RES | 1
0 |  | R5, R6 | 0805 | RESISTOR0805-RES | 2
124 |  | R7 | 0805 | RESISTOR0805-RES | 1
4.7K |  | R11 | 0805 | RESISTOR0805-RES | 1
47k |  | R12 | 0805 | RESISTOR0805-RES | 1
FSMSMTR | SWITCH TACTILE SPST-NO 0.05A 24V | S1 | TE FSMSMTR | FSMSMTR | 1
ATmega328P-AU | 8-bit AVR Microcontroller, 32KB Flash, 1KB EEPROM, 2KB SRAM, 32-pin TQFP, Industrial Grade (-40°C to 85°C) | U1 | 32A_N | ATmega328P-AU | 1
16MHz | CRYSTAL 16.0000MHZ 8PF SMD | Y1, Y2 | NDK NX3225SA | NX3225SA-16.000MHZ-STD-CSR-1 | 2

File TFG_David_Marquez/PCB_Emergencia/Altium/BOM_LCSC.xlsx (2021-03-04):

LCSC Part Number | Manufacture Part Number | Manufacturer | Customer NO. | Package | Description | RoHS | Order Qty. | Min\Mult Order Qty. | Unit Price | Order Price
C3002 | IRF7832TRPBF | International Rectifier |  | SOIC-8_150mil | MOSFET N Trench 30V 20A 2.32V @ 250uA 4 mΩ @ 20A,10V SOIC-8_150mil RoHS | Yes | 3 | 1\1 | $0.5227 | $1.57
C7376 | MCP2551-I/SN | Microchip Tech |  | SOIC-8_150mil | CAN 1/1 4.5V ~ 5.5V SOIC-8_150mil RoHS | Yes | 3 | 1\1 | $0.7561 | $2.27
C13738 | X322516MLB4SI | Yangxing Tech |  | SMD-3225_4P | SMD Crystal Resonators 16MHz ±10ppm SMD-3225_4P RoHS | Yes | 5 | 5\5 | $0.095 | $0.48
C13879 | MF52A103F3950(A1) | Nanjing Shiheng Elec |  | Through Hole,P=1.7mm | NTC Thermistors 1/20W 10KOhms ±1% 3950K Through Hole,P=1.7mm RoHS | Yes | 10 | 10\10 | $0.0457 | $0.46
C84376 | RC0805FR-0710KL | YAGEO |  | 0805 | Chip Resistor - Surface Mount 10KOhms ±1% 1/8W 0805 RoHS | Yes | 100 | 100\100 | $0.0017 | $0.17
C84817 | MT3608 | XI'AN Aerosemi Tech |  | SOT-23-6 | DC-DC Converters Step-Up Adjustable 1 2V 24V 28V SOT-23-6 RoHS | Yes | 10 | 5\5 | $0.0795 | $0.8
C90266 | RVT2A4R7M0605 | ROQANG |  | SMD,6.3x5.4mm | Aluminum Electrolytic Capacitors - SMD 4.7uF ±20% 100V SMD,6.3x5.4mm RoHS | Yes | 10 | 10\10 | $0.0333 | $0.34
C98190 | CL21A226MOQNNNE | Samsung Electro-Mechanics |  | 0805 | Multilayer Ceramic Capacitors MLCC - SMD/SMT 22uF 16V 0805 RoHS | Yes | 20 | 10\10 | $0.0382 | $0.77
C103901 | RTT05000JTP | RALEC |  | 0805 | Chip Resistor - Surface Mount 0Ohms ±5% 1/8W 0805 RoHS | Yes | 100 | 100\100 | $0.0023 | $0.23
C103956 | RTT05122JTP | RALEC |  | 0805 | Chip Resistor - Surface Mount 1.2KOhms ±5% 1/8W 0805 RoHS | Yes | 50 | 50\50 | $0.0019 | $0.1
C118936 | 3296W-1-203 | Chengdu Guosheng Tech |  | 3296W | Precision Potentiometer 20KOhms ±10% ±100ppm/℃ 3296W RoHS | Yes | 5 | 5\5 | $0.1333 | $0.67
C133406 | CDRH74-220MT | Meled Industrial |  | 7*7*4 | Power Inductors 22uH ±20% 1.23A 7*7*4 RoHS | Yes | 5 | 5\5 | $0.1124 | $0.57
C136740 | C136740 | Korean Hroparts Elec |  | 6*3.3mm | Tactile Switches SPST-NO 6.00mm x 3.30mm 4.30mm 50mA @ 12VDC 6*3.3mm RoHS | Yes | 10 | 10\10 | $0.0565 | $0.57
C149532 | SMMS1360-680M | Shun Xiang Nuo Elec |  | SMD,13.8x12.6x7mm | Power Inductors 68uH ±20% 3.5A SMD,13.8x12.6x7mm RoHS | Yes | 5 | 1\1 | $0.5136 | $2.57
C153782 | MCP2515T-I/SO | Microchip Tech |  | SOIC-18 | CAN 2.7V ~ 5.5V SOIC-18 RoHS | Yes | 3 | 1\1 | $1.2985 | $3.9
C161863 | PAP-02V-S | JST Sales America |  | Housing,P=2mm | Rectangular Connectors Housings Housing,P=2mm RoHS | Yes | 10 | 10\10 | $0.0485 | $0.49
C162422 | GRM21BR6YA106KE43L | Murata Electronics |  | 0805 | Multilayer Ceramic Capacitors MLCC - SMD/SMT 10uF 35V 0805 RoHS | Yes | 20 | 5\5 | $0.0814 | $1.63
C183996 | SS26FL | Shikues |  | SMAF | Schottky Barrier Diodes (SBD) SMAF RoHS | Yes | 10 | 10\10 | $0.0332 | $0.34
C240844 | 53015-0210 | MOLEX |  | Through Hole | Wire To Board / Wire To Wire Connector Through Hole RoHS | Yes | 5 | 5\5 | $0.0595 | $0.3
C247134 | 0805W8F400LT5E | Uniroyal Elec |  | 0805 | Chip Resistor - Surface Mount 0.4Ohms ±1% 1/8W 0805 RoHS | Yes | 50 | 50\50 | $0.003 | $0.15
C265094 | S02B-PASK-2(LF)(SN) | JST Sales America |  | Through Hole,P=2mm | Wire To Board / Wire To Wire Connector Through Hole,P=2mm RoHS | Yes | 5 | 1\1 | $0.1183 | $0.6
C340931 | LM2596S-5.0/TR | Huaguan Semicon |  | TO-263-5 | DC-DC Converters TO-263-5 RoHS | Yes | 10 | 1\1 | $0.1909 | $1.91
C382139 | TP4056 | TPOWER |  | ESOP-8 | PMIC - Battery Management ESOP-8 RoHS | Yes | 10 | 5\5 | $0.0712 | $0.72

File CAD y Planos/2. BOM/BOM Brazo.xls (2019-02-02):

Recapitulation of: Robot_Rigido_7_Sec
Different parts: 13
Total parts: 1211
Quantity | Part Number
7 | Cardan_57mm
14 | Base_Rigida
14 | Base_Cardan
28 | Separador_Fijo
28 | Soporte_Cardan
28 | 4762_SCREW_M3x6
28 | 7093_WASHER_3x9
56 | Escuadrilla
84 | 10511_NUT_M4
84 | 10642_SCREW_M4x12
84 | 4762_SCREW_M4x8
252 | Guia_Cables
504 | Casquillo

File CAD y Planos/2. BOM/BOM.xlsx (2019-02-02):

Recapitulation of: Robot+Base
Different parts: 79
Total parts: 3768
Quantity | Part Number
312 | 10511_NUT_M3
176 | 10511_NUT_M4
240 | 10642_SCREW_M3x12
92 | 10642_SCREW_M4x12
68 | 10642_SCREW_M4x16
48 | 10642_SCREW_M4x20
24 | 10642_SCREW_M4x8
28 | 1587_M4_Tuerca_Ciega
24 | 4026_SCREW_M6x20
24 | 4032_NUT_M6
144 | 4762_SCREW_M3x12
72 | 4762_SCREW_M3x16
28 | 4762_SCREW_M3x6
84 | 4762_SCREW_M3x8
282 | 4762_SCREW_M4x10
8 | 4762_SCREW_M4x12
28 | 4762_SCREW_M4x16
212 | 4762_SCREW_M4x20
114 | 4762_SCREW_M4x8
60 | 623VV
120 | 7091_WASHER_3x7
28 | 7093_WASHER_3x9
24 | BA6_Bearing
14 | Base_Cardan
14 | Base_Rigida
7 | Cardan_57mm
504 | Casquillo
24 | CHP-36GP-555
24 | Coupling 8x8
24 | End-Stop
56 | Escuadrilla
252 | Guia_Cables
48 | LMF_12
8 | Pata_Ext
20 | Pata_Inter
2 | PCB_Alimentacion
24 | PCB_Control_Motores
16 | Pestana_Anclaje
1 | Placa_Aclople_Robot
2 | Placa_Colector
2 | Placa_Colector_2
2 | Placa_Colector_2_2
1 | Placa_Conversor_Grand
1 | Placa_Conversor_Grand_2
1 | Placa_Conversor_Grand_2_Ext
1 | Placa_Conversor_Grand_Ext
1 | Placa_Conversor_Peq
1 | Placa_Conversor_Peq_2
1 | Placa_FdC
24 | Placa_Intermedia
2 | PlacaSoporte_Electronica_Exterior
1 | PlacaSoporte_Electronica_Interior
2 | PlacaSoporte_Motor
2 | PlacaSoporteExterior_Libre
2 | PlacaSoporteExterior_Libre_Tapa
2 | PlacaSoporteExterior_Motor
2 | PlacaSoporteExterior_Motor_Tapa
1 | PlacaSoporteInterior_Libre
1 | PlacaSoporteInterior_Libre_2
1 | PlacaSoporteInterior_Motor
1 | PlacaSoporteInterior_Motor_2
1 | PlacaSoporteInterior_Motor_3
28 | Separador_Fijo
84 | Separador_PCB
14 | Separador_Placa_Motores
4 | Separador_Placa_Motores_Interna
4 | Separador_Placa_Motores_Interna_2
88 | Separador_Poleas_Central
24 | Separador_Poleas_Central_Large
8 | Separador_Poleas_Central_Peq
12 | Separador_Soporte_PCB_FdC
28 | Soporte_Cardan
24 | Soporte_End_Stop
3 | Soporte_PCB_FdC
24 | TR10
24 | Tuerca_Tr10
12 | Varilla12x130
4 | Varilla12x30
50 | Varilla12x483
66

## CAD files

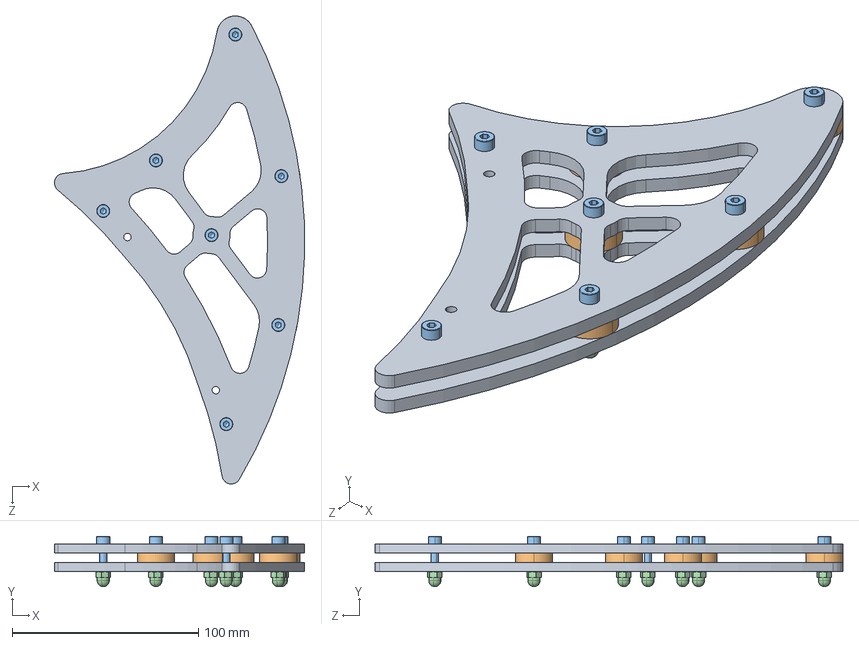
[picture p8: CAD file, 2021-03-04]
TFG_David_Marquez/Eje Z/Pata Mach I/Montaje_Pata_Robot.SLDASM
134.5 x 27.0 x 251.5 mm
Pata_Ext.CATPart x 2
Pata_Inter.CATPart x 5
ISO_4762_M4x20_STEEL_HEXAGON_SOCKET_HEAD_CAP_SCREW.CATPart x 7
1587_M4_Tuerca_Ciega.CATPart x 7

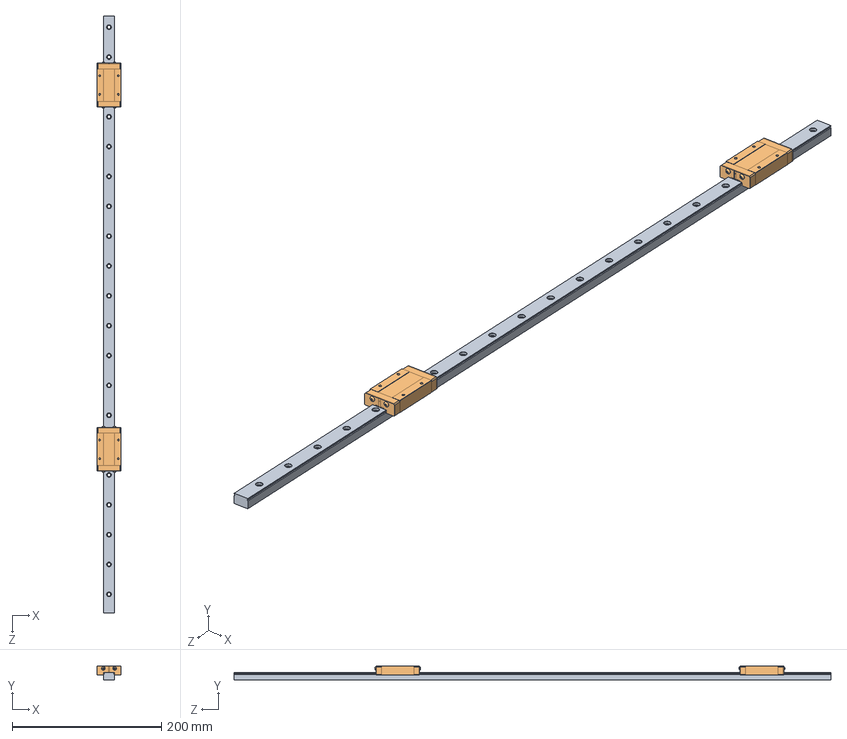
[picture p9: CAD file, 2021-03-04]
TFG_David_Marquez/Eje Z/Guías lineales/MGN15_AND_RAIL.SLDASM
32.0 x 18.8 x 800.0 mm
MGN15 rail
MGN15C x 2

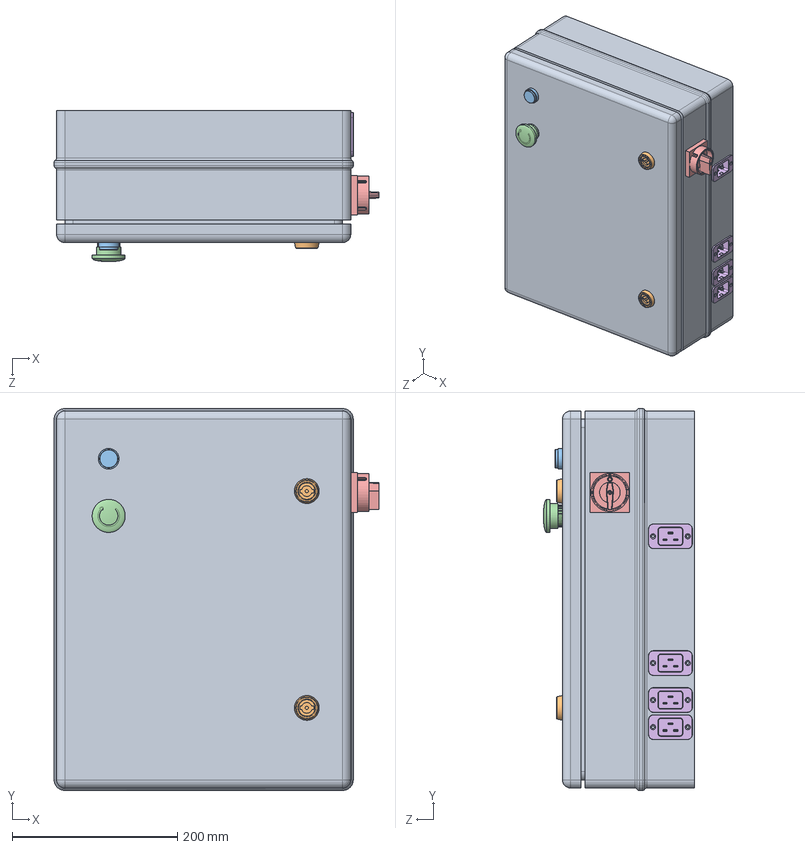
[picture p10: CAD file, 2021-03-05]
TFG_David_Marquez/Unity/Modelos/Armario/Armario.SLDASM
393.0 x 462.0 x 183.0 mm
Caja
Cerradura x 2
LED Status -G
E-Stop Button [ZB4BS844]
Lovato GX15 690V 16A Isolator Switch Model
Einbau-Gerätestecker 24V_16A.step x 4

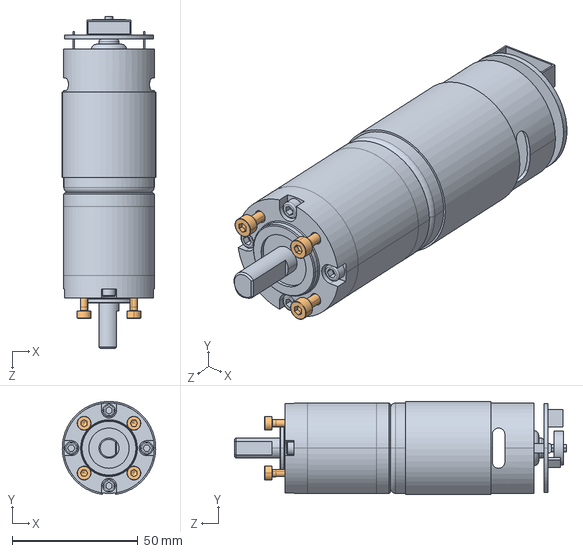
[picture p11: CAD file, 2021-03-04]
TFG_David_Marquez/Eje Z/Motor_Tornillos.SLDASM
37.2 x 37.0 x 132.0 mm
CHP-36GP-555.CATPart
ISO_4762_M3x12_STEEL_HEXAGON_SOCKET_HEAD_CAP_SCREW.CATPart x 4

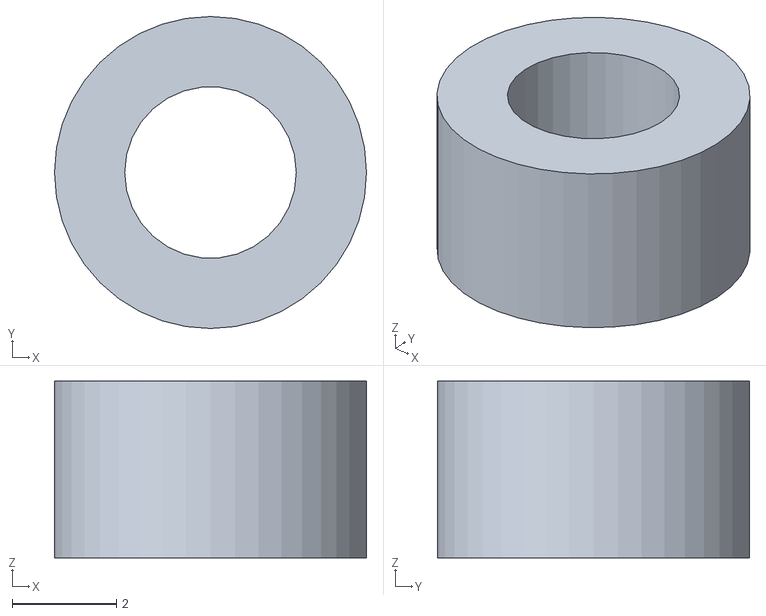
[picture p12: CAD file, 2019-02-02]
CAD y Planos/0. MACH I/Piezas_Impresas/Separador_PCB.stl
6.00 x 6.00 x 3.40

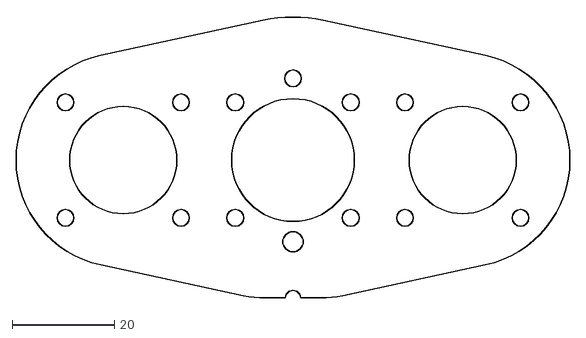
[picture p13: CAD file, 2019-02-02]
CAD y Planos/3. Planos de corte/10mmAlu/24pcs_10mm_Al_Placa_Intermedia.dxf
108.5 x 55.2

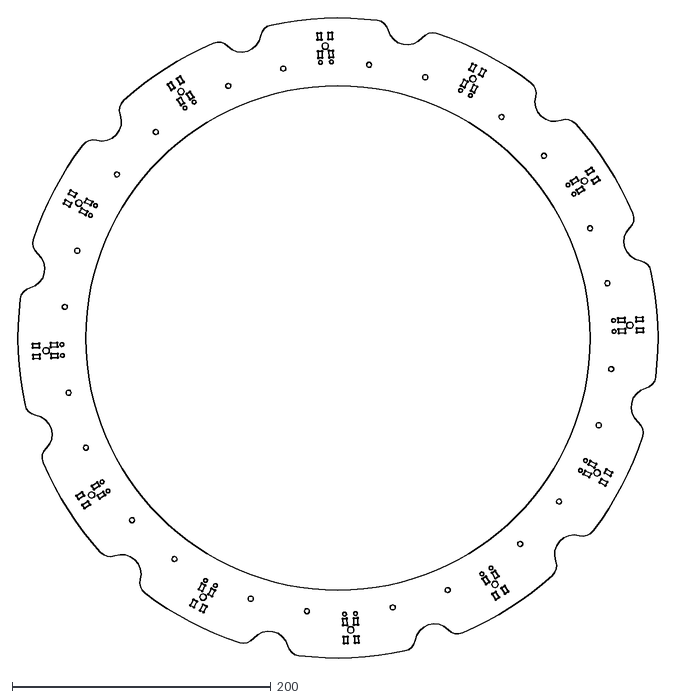
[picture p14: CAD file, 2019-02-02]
CAD y Planos/3. Planos de corte/3mmSteel/1pcs_3mm_St_Placa_Conversor_Grand_2_Ext.dxf
498.0 x 498.0

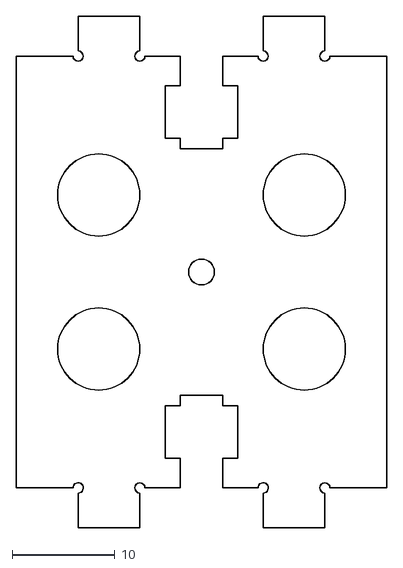
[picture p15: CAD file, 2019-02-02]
CAD y Planos/3. Planos de corte/4mmAlu/28pcs_4mm_Al_Separador_Fijo.dxf
36.0 x 49.8

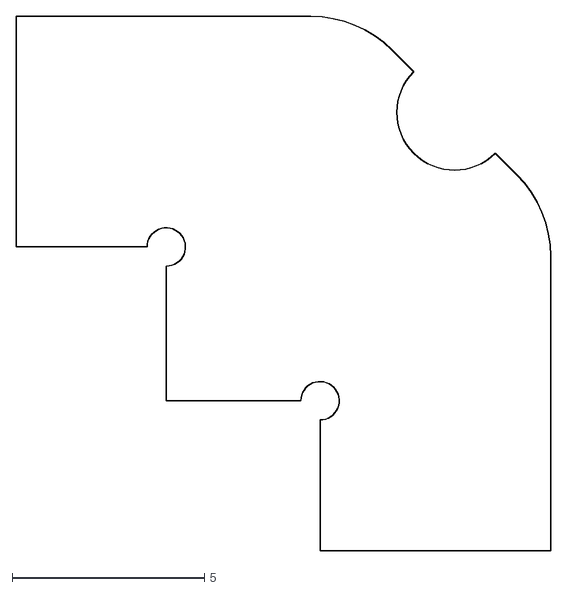
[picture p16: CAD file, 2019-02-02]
CAD y Planos/3. Planos de corte/4mmSteel/20pcs_4mm_St_Escuadrilla.dxf
13.9 x 13.9

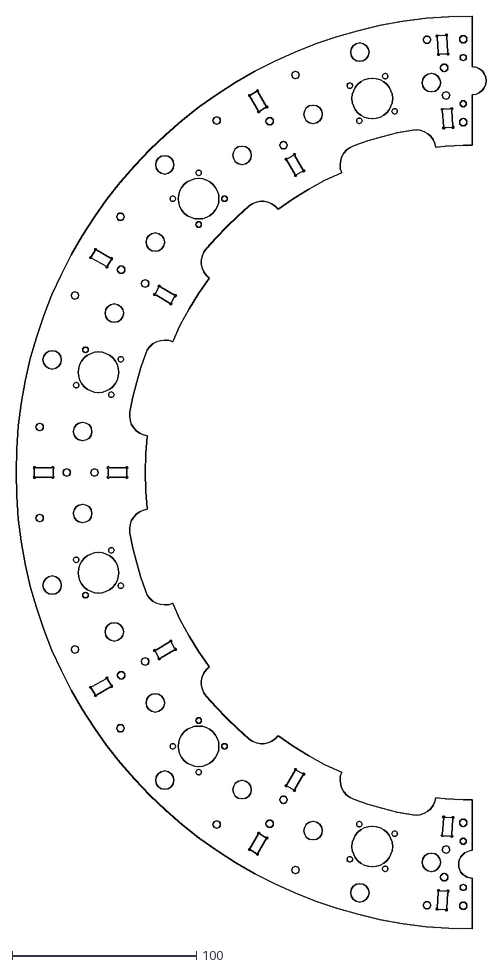
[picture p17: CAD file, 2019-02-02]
CAD y Planos/3. Planos de corte/5mmSteel/2pcs_5mm_St_PlacaSoporte_Motor.dxf
255.3 x 495.0

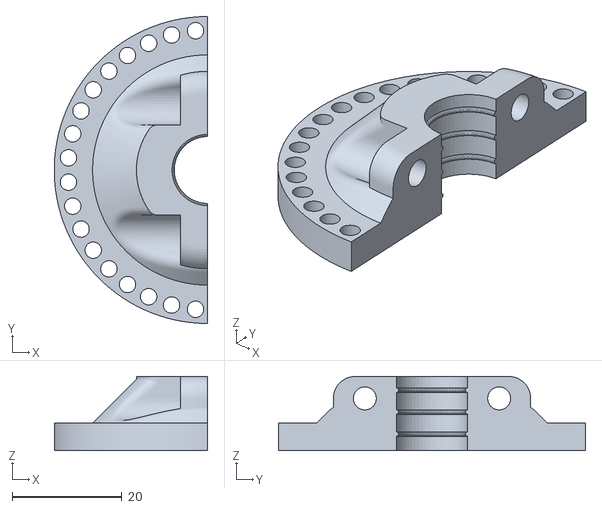
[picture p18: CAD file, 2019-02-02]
CAD y Planos/Discontinued/Prototipo_2_56mm/Acople_Robot_Flexible_Guia.stl
28.0 x 56.0 x 13.5

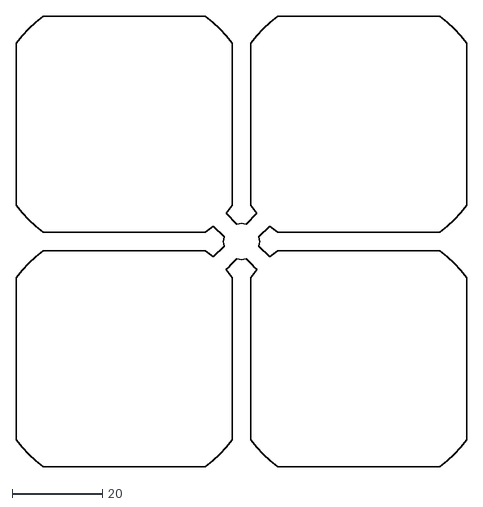
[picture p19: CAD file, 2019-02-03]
PCBs/Discontinued/PCB Motor/CATIA_Contorno_4.dxf
100.0 x 100.0

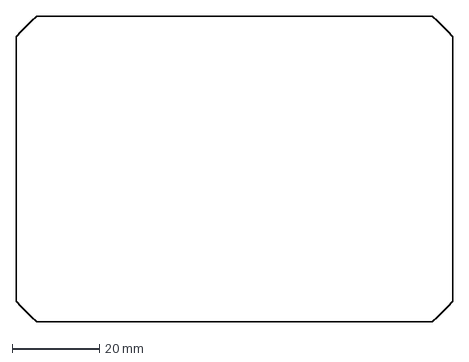
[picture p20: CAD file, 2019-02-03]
PCBs/PCB Alimentacion 24V/PCB_Contorno.dxf
100.0 x 70.0 mm

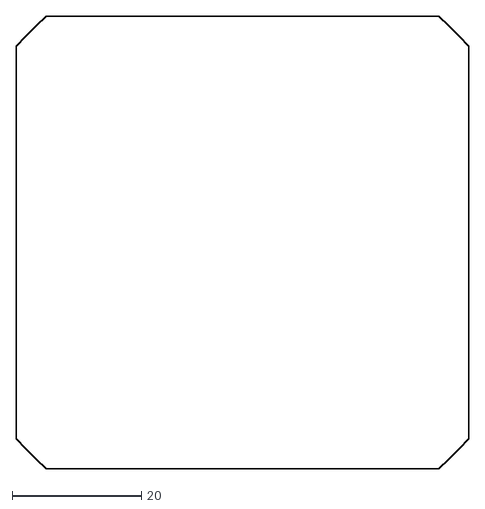
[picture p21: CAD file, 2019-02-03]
PCBs/PCB Alimentacion 9V/Catia.dxf
70.0 x 70.0

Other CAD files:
PCBs/PCB FdC/CATIA.dxf
TFG_David_Marquez/Eje Z/Guías lineales/MGN15C.STEP
CAD y Planos/0. MACH I/0. Discontinued/BA_6/BA_6.CATProduct
CAD y Planos/0. MACH I/0. Discontinued/BA_6/BA_6_PART1.CATPart
CAD y Planos/0. MACH I/0. Discontinued/BA_6/BA_6_PART2.CATPart
CAD y Planos/0. MACH I/0. Discontinued/BA_6/BA_6_PART3.CATPart
CAD y Planos/0. MACH I/0. Discontinued/BA_6/BA_6_PART4.CATPart
CAD y Planos/0. MACH I/0. Discontinued/Brushless_Motor.CATPart
CAD y Planos/0. MACH I/0. Discontinued/Encoder E6B2-CWZ6C/E6B2-CWZ6C-1.CATPart
CAD y Planos/0. MACH I/0. Discontinued/Encoder E6B2-CWZ6C/E6B2-CWZ6C-2.CATPart
CAD y Planos/0. MACH I/0. Discontinued/Encoder E6B2-CWZ6C/E6B2-CWZ6C-3.CATPart
CAD y Planos/0. MACH I/0. Discontinued/Encoder E6B2-CWZ6C/E6B2-CWZ6C.CATProduct
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

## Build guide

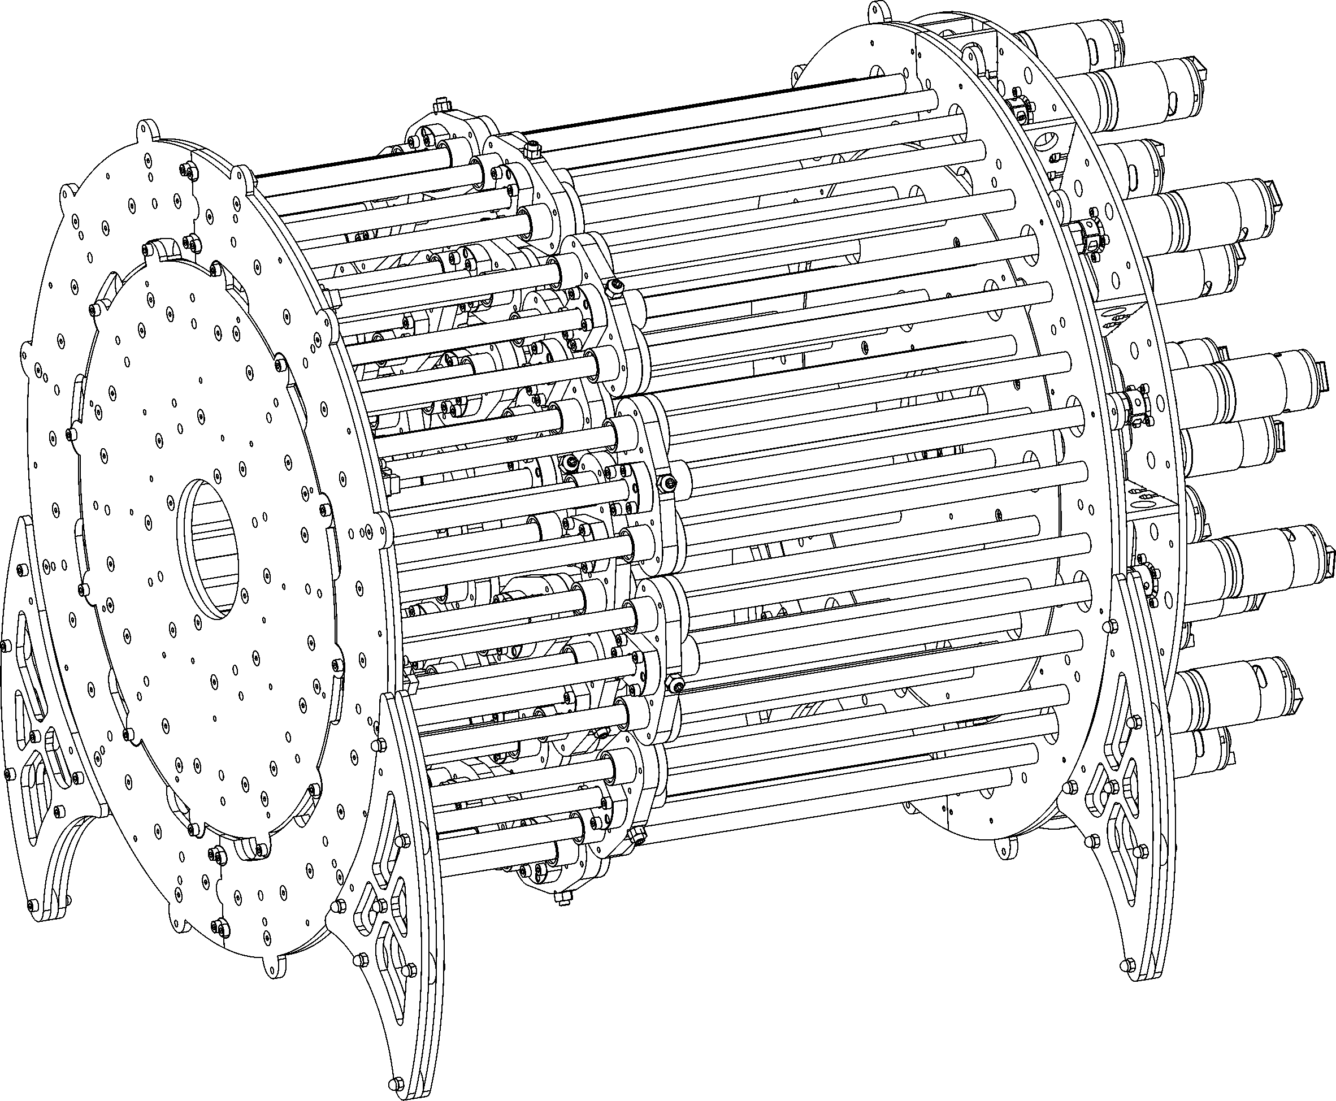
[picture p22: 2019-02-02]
Renders/Montaje_Estructura.png

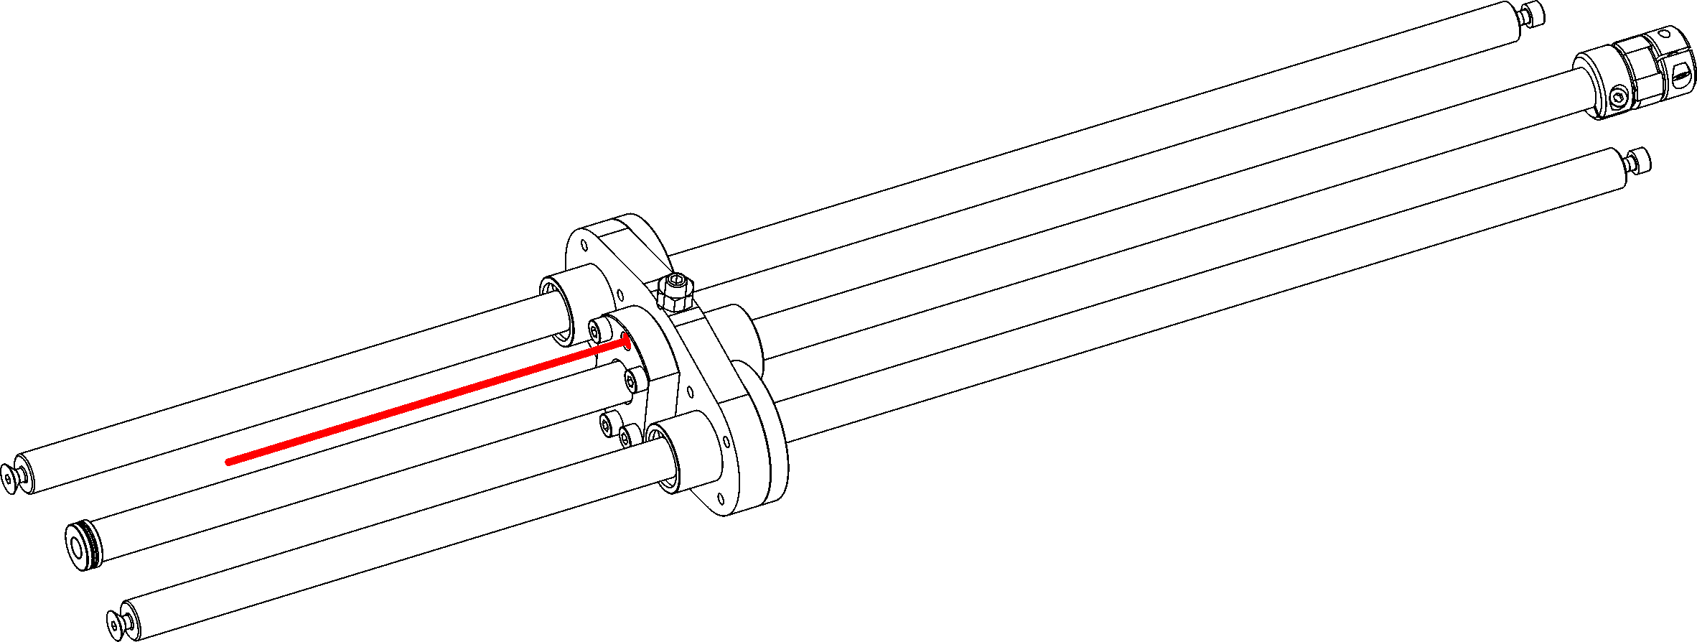
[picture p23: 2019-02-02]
Renders/Montaje_Husillo.png

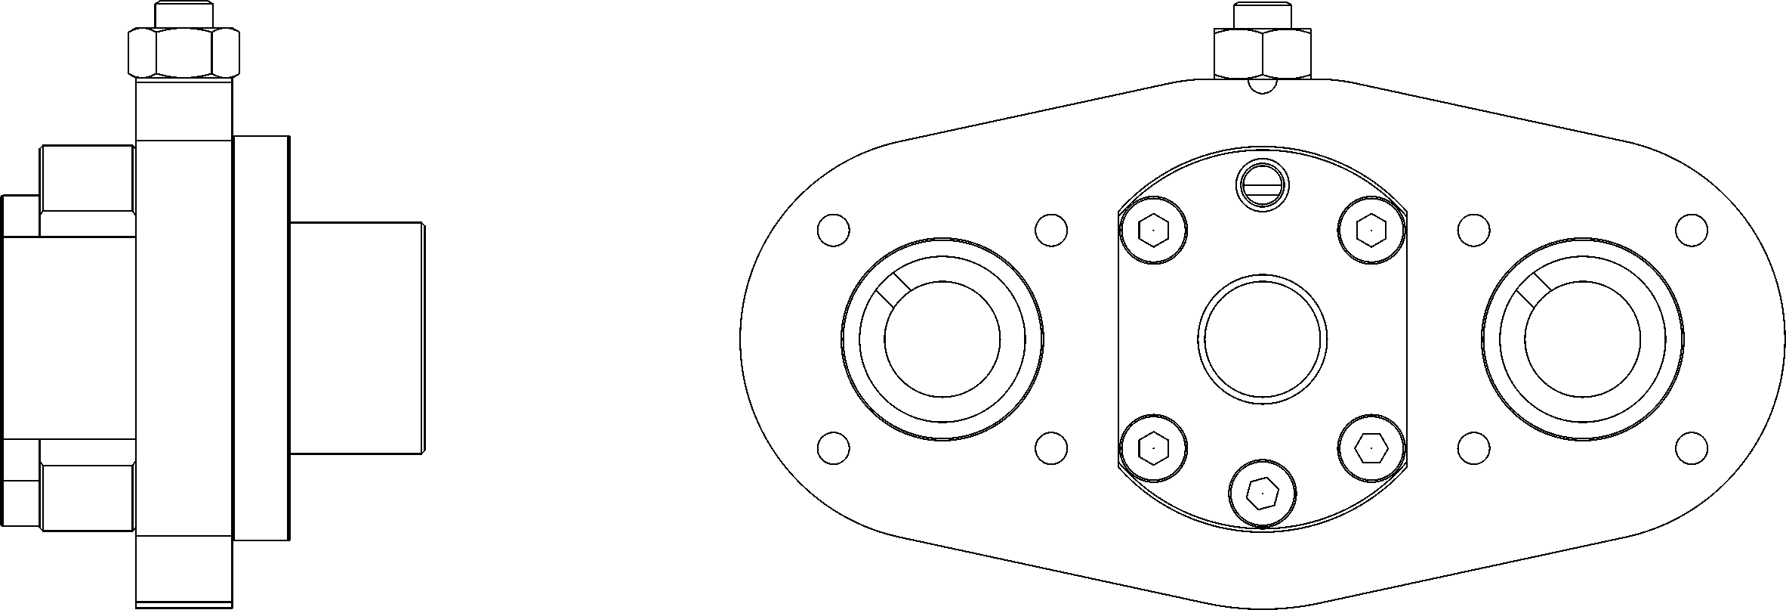
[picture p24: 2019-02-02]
Renders/Montaje_Carro.png

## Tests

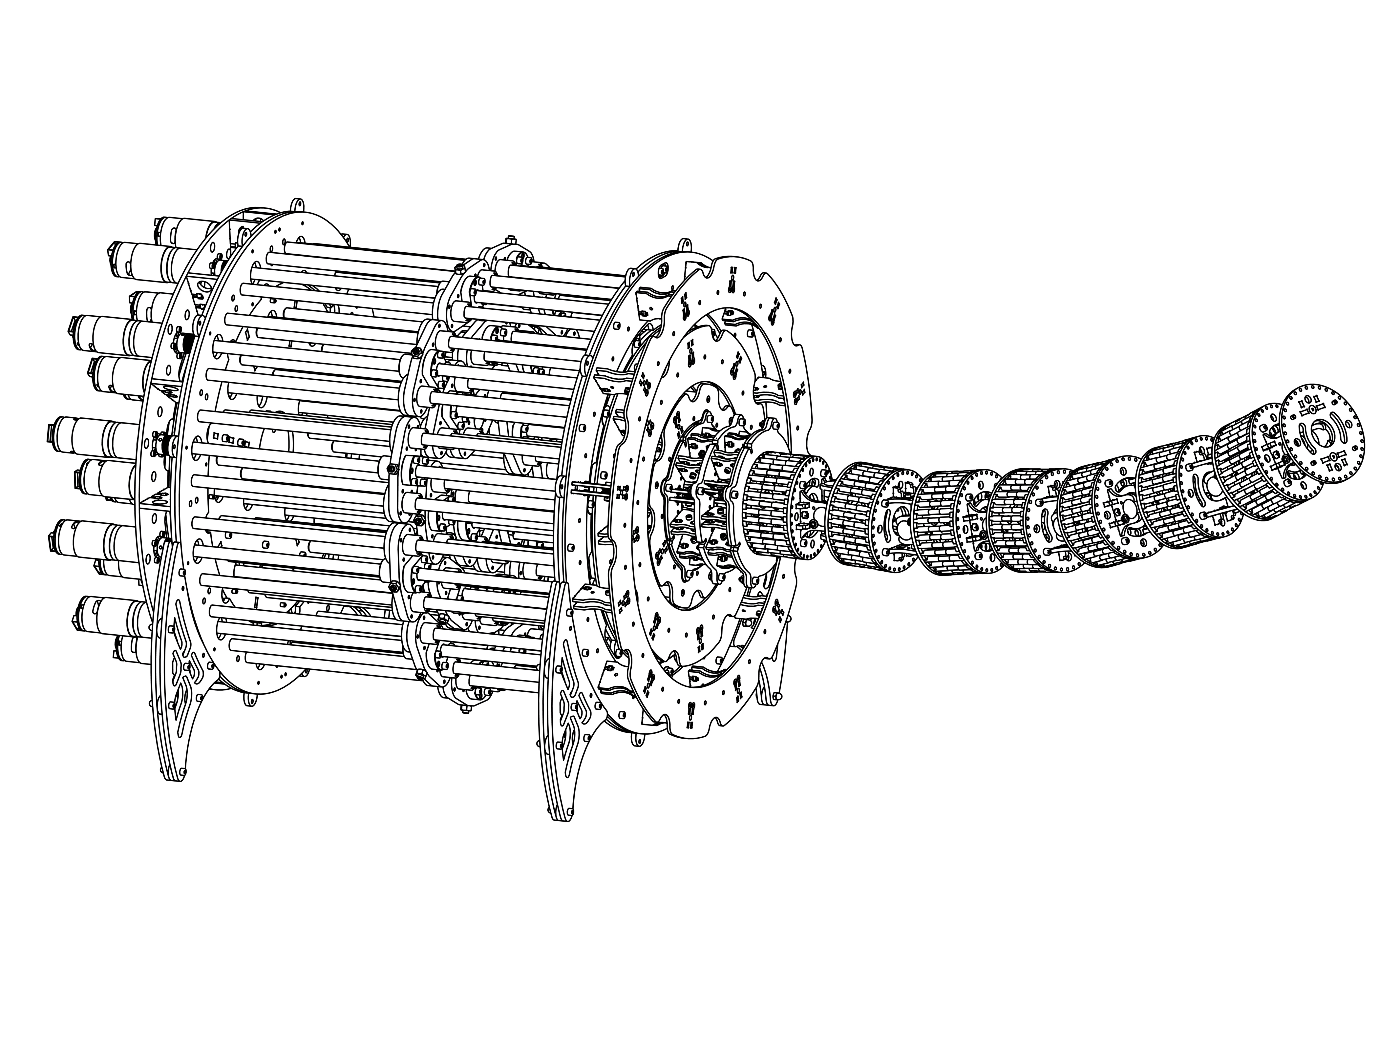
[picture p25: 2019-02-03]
Renders/Prueba.jpg

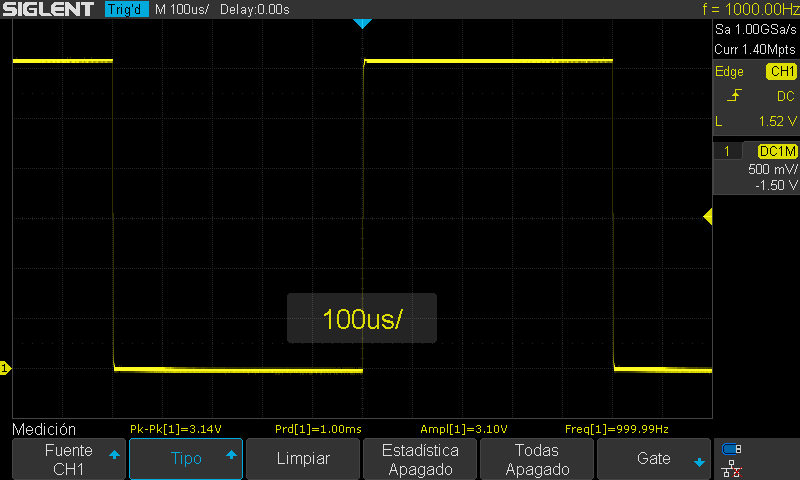
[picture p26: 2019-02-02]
Programas/Arduino/Pruebas_Osciloscopio/SDS00002.png

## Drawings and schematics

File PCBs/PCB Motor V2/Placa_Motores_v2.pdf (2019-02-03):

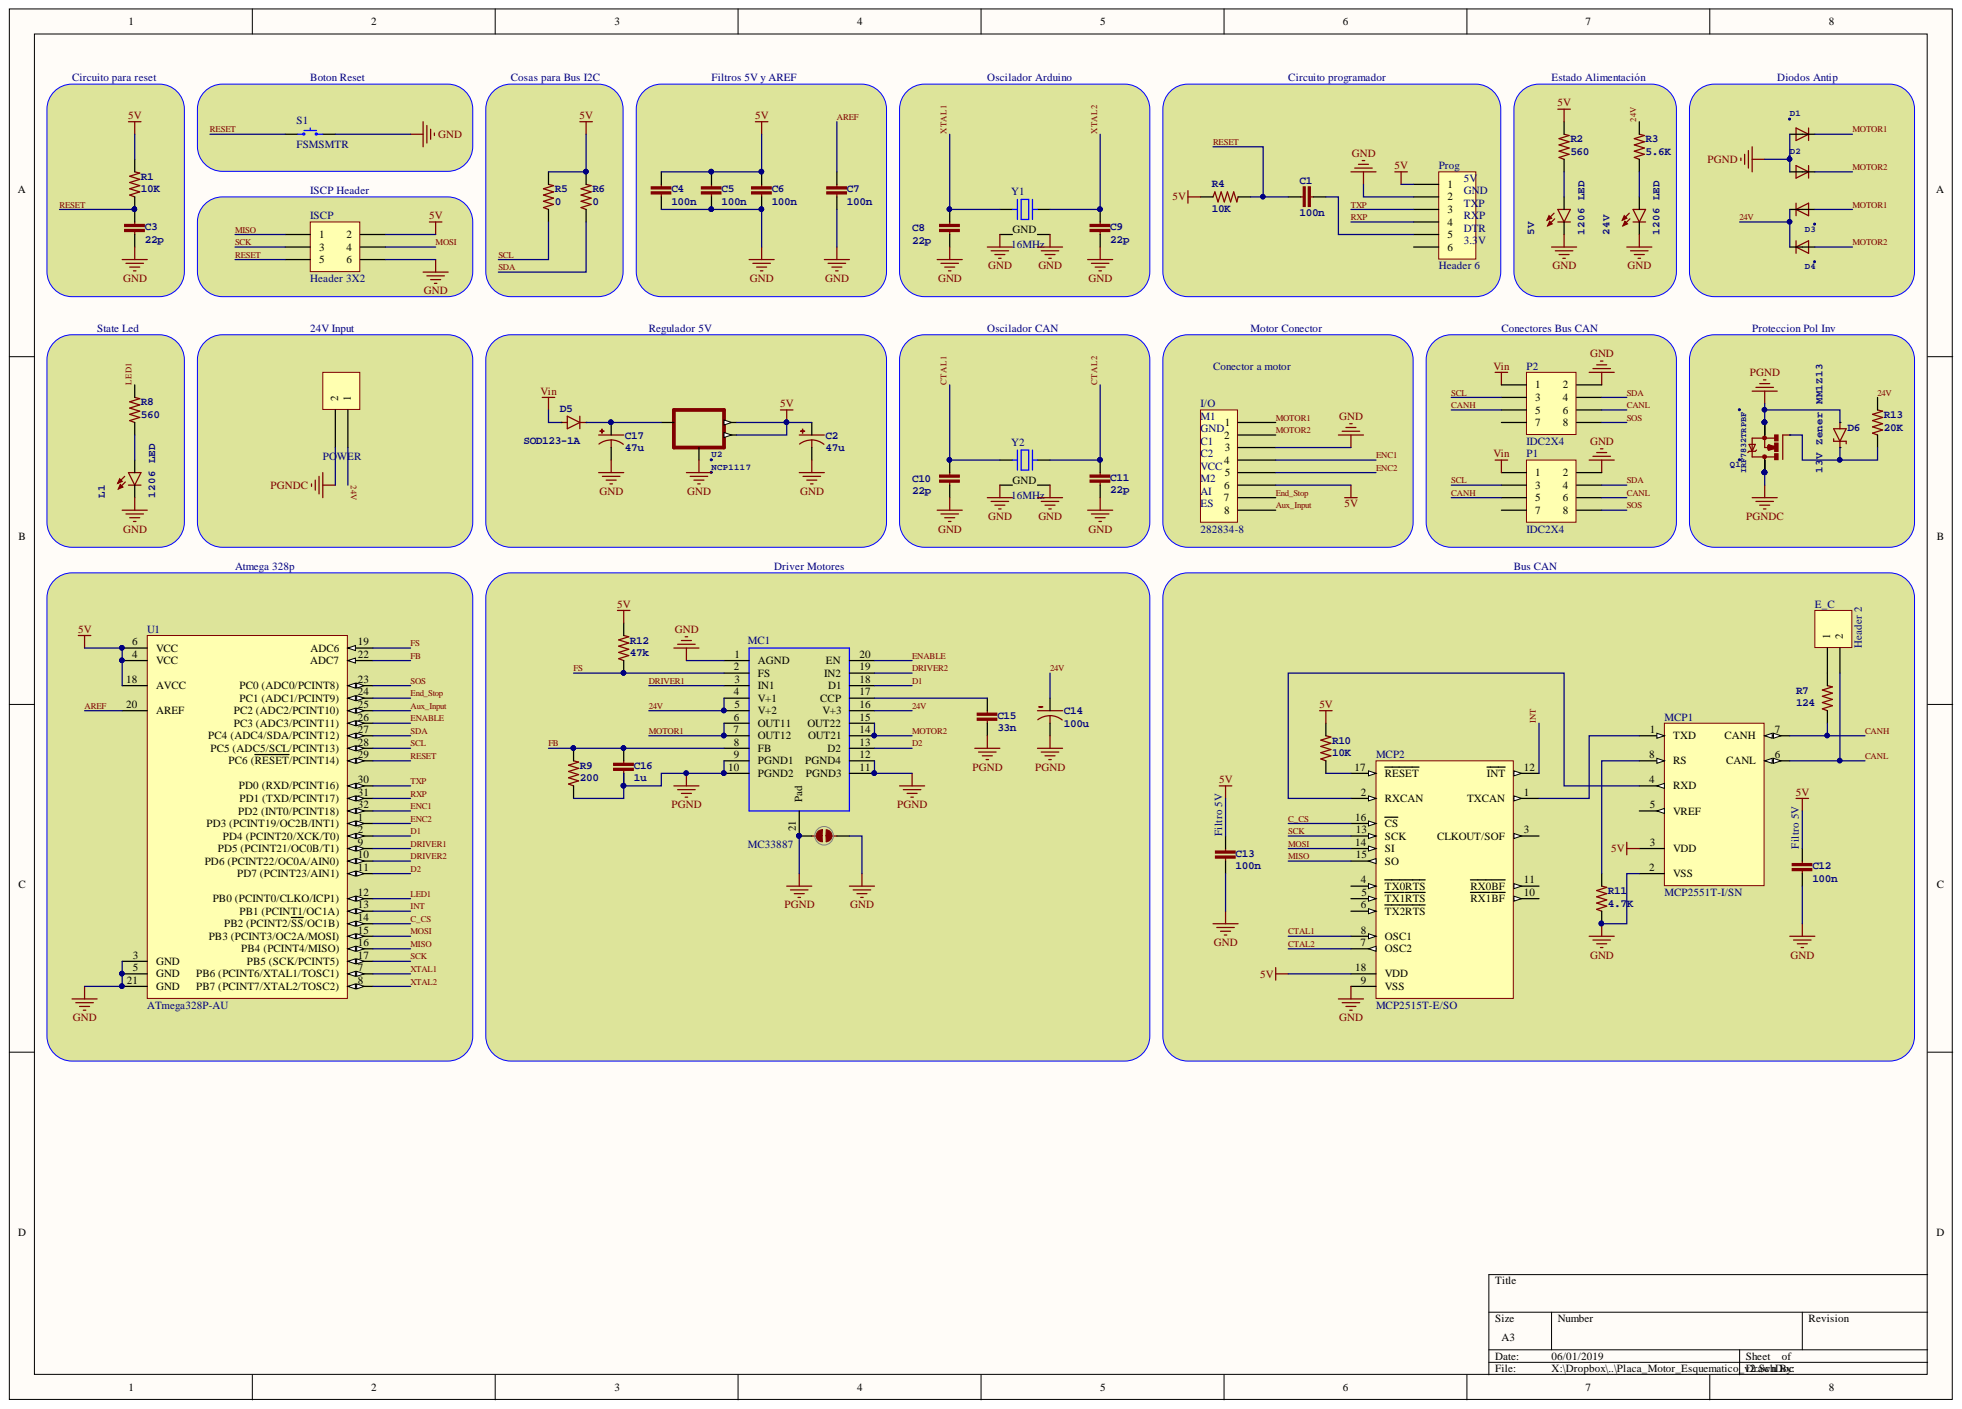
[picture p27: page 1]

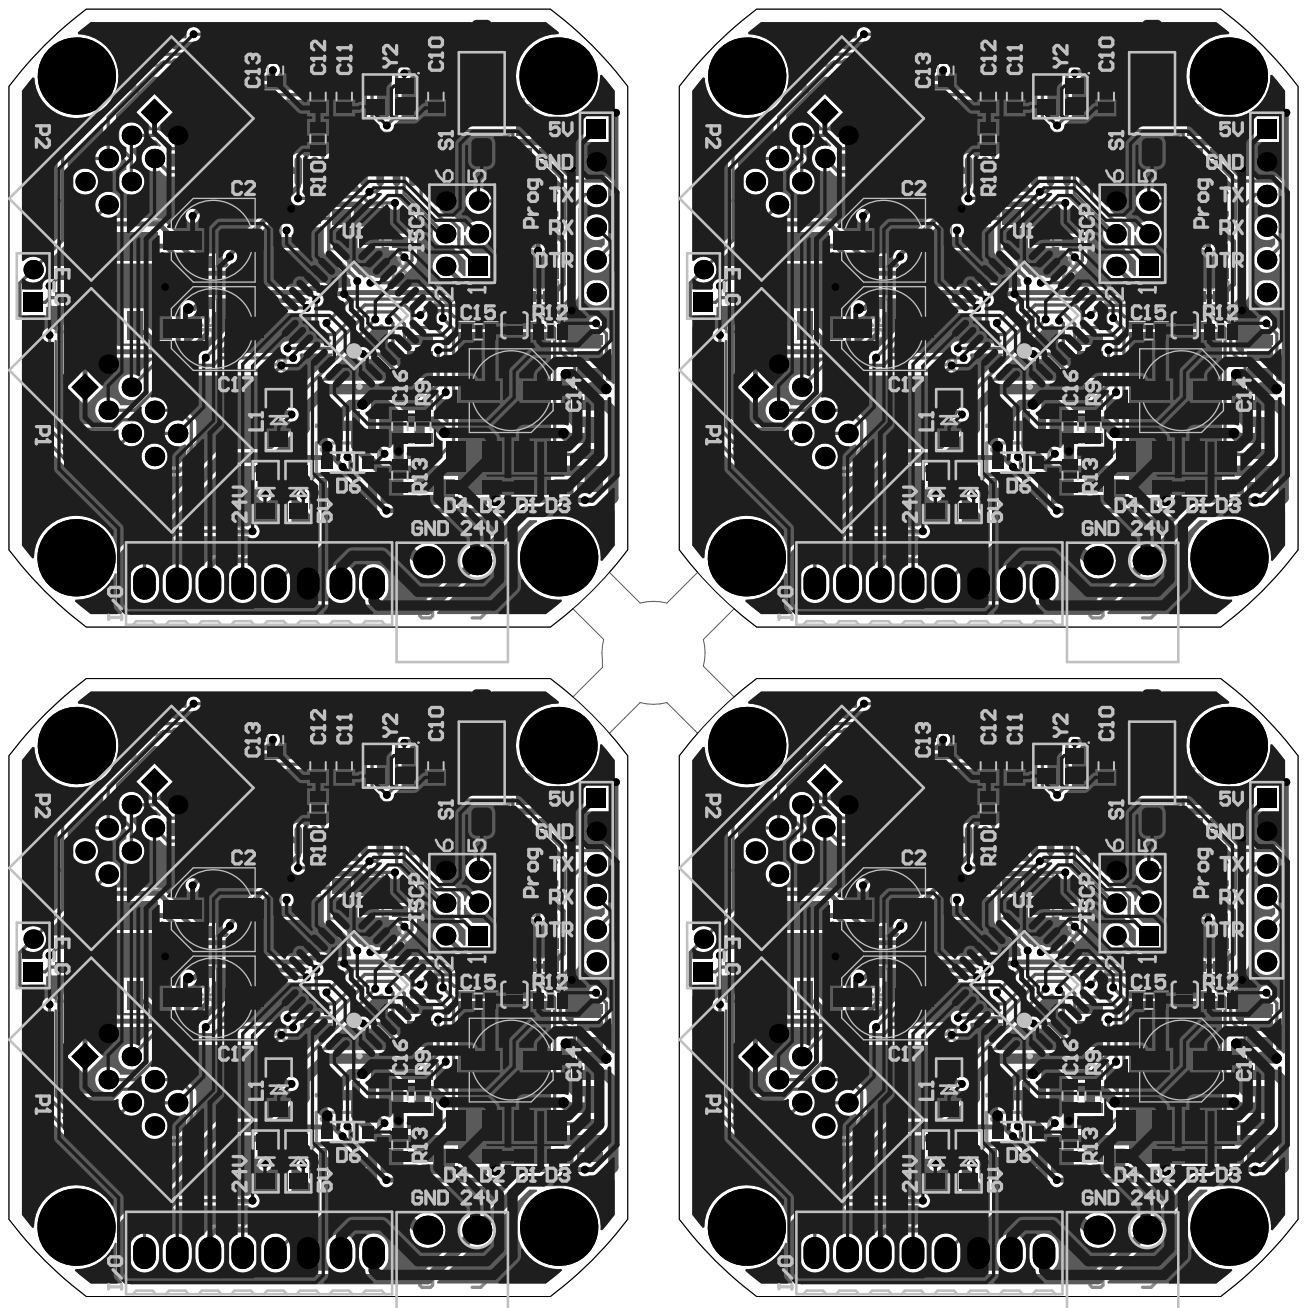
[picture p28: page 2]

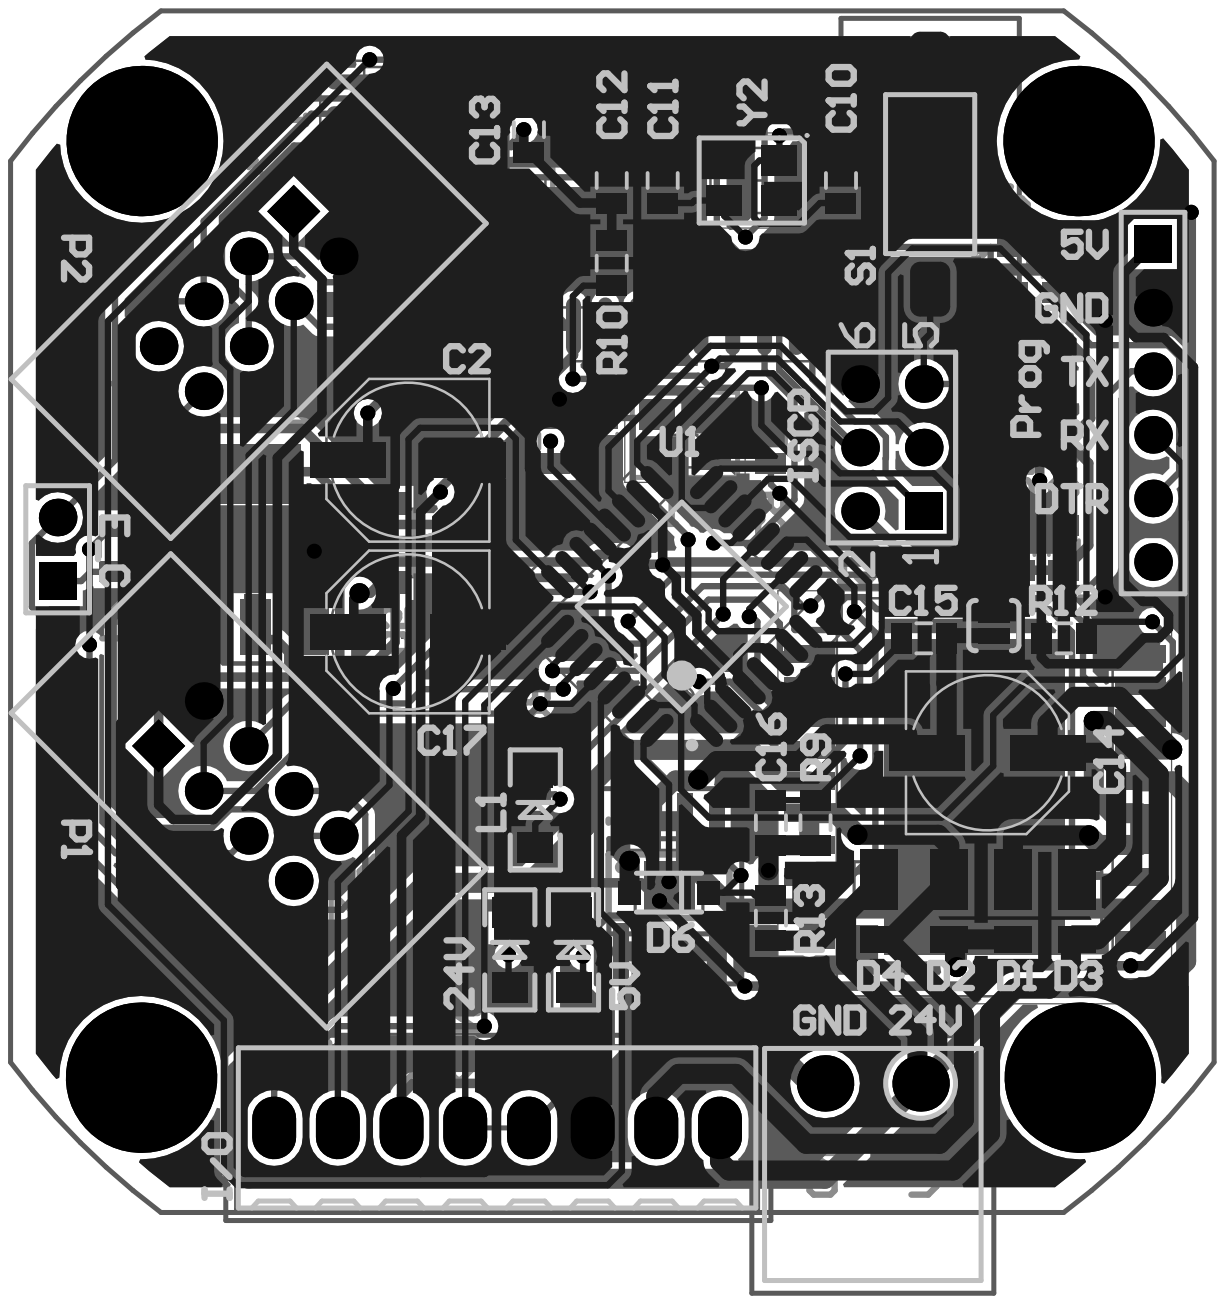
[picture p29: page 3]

# Board S

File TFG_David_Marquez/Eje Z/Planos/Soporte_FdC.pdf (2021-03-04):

22,50

45,00

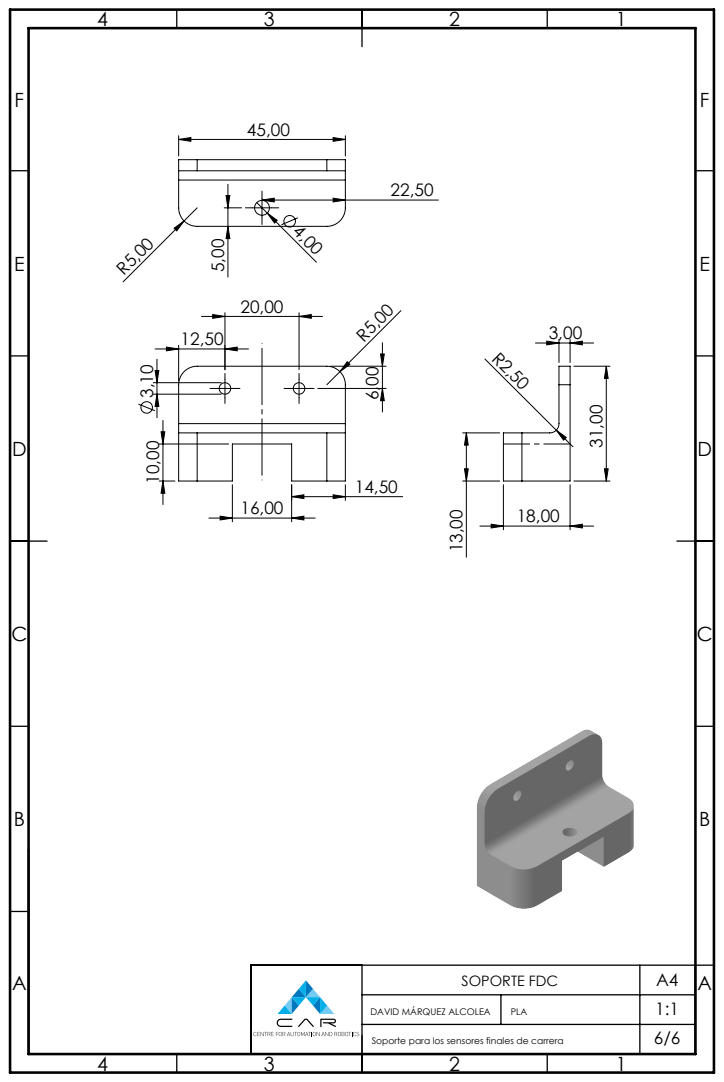
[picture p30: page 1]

SOPORTE FDC | A4

DAVID MÁRQUEZ ALCOLEA | PLA | 1:1

Soporte para los sensores finales de carrera | | 6/6

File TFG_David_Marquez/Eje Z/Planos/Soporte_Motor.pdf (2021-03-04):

E | E
F | F

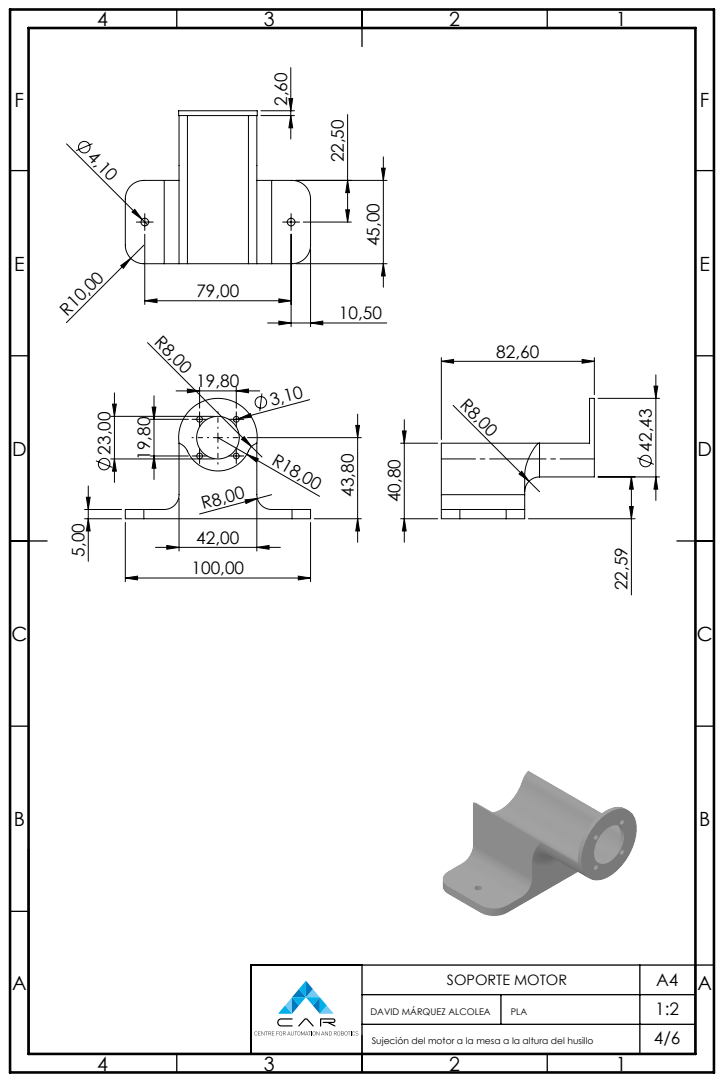
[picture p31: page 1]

SOPORTE MOTOR | A4

DAVID MÁRQUEZ ALCOLEA | PLA | 1:2

Sujeción del motor a la mesa a la altura del husillo | | 4/6

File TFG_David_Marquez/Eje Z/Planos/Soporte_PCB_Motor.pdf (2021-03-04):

37,41

5,00

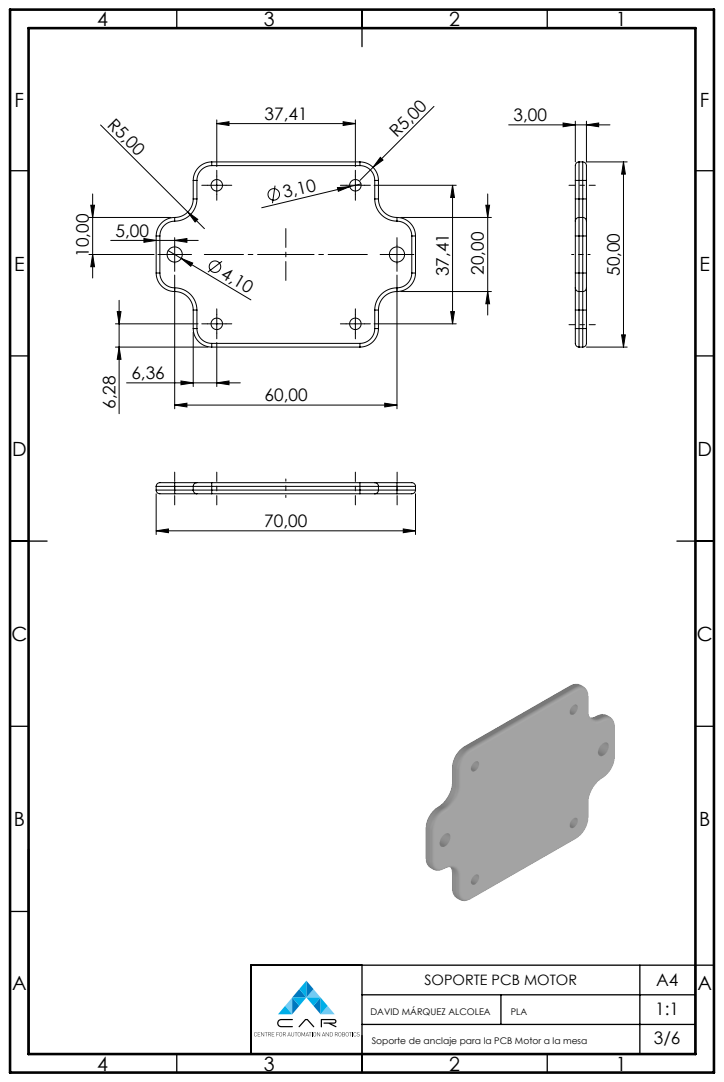
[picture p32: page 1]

SOPORTE PCB MOTOR | A4

DAVID MÁRQUEZ ALCOLEA | PLA | 1:1

Soporte de anclaje para la PCB Motor a la mesa | | 3/6

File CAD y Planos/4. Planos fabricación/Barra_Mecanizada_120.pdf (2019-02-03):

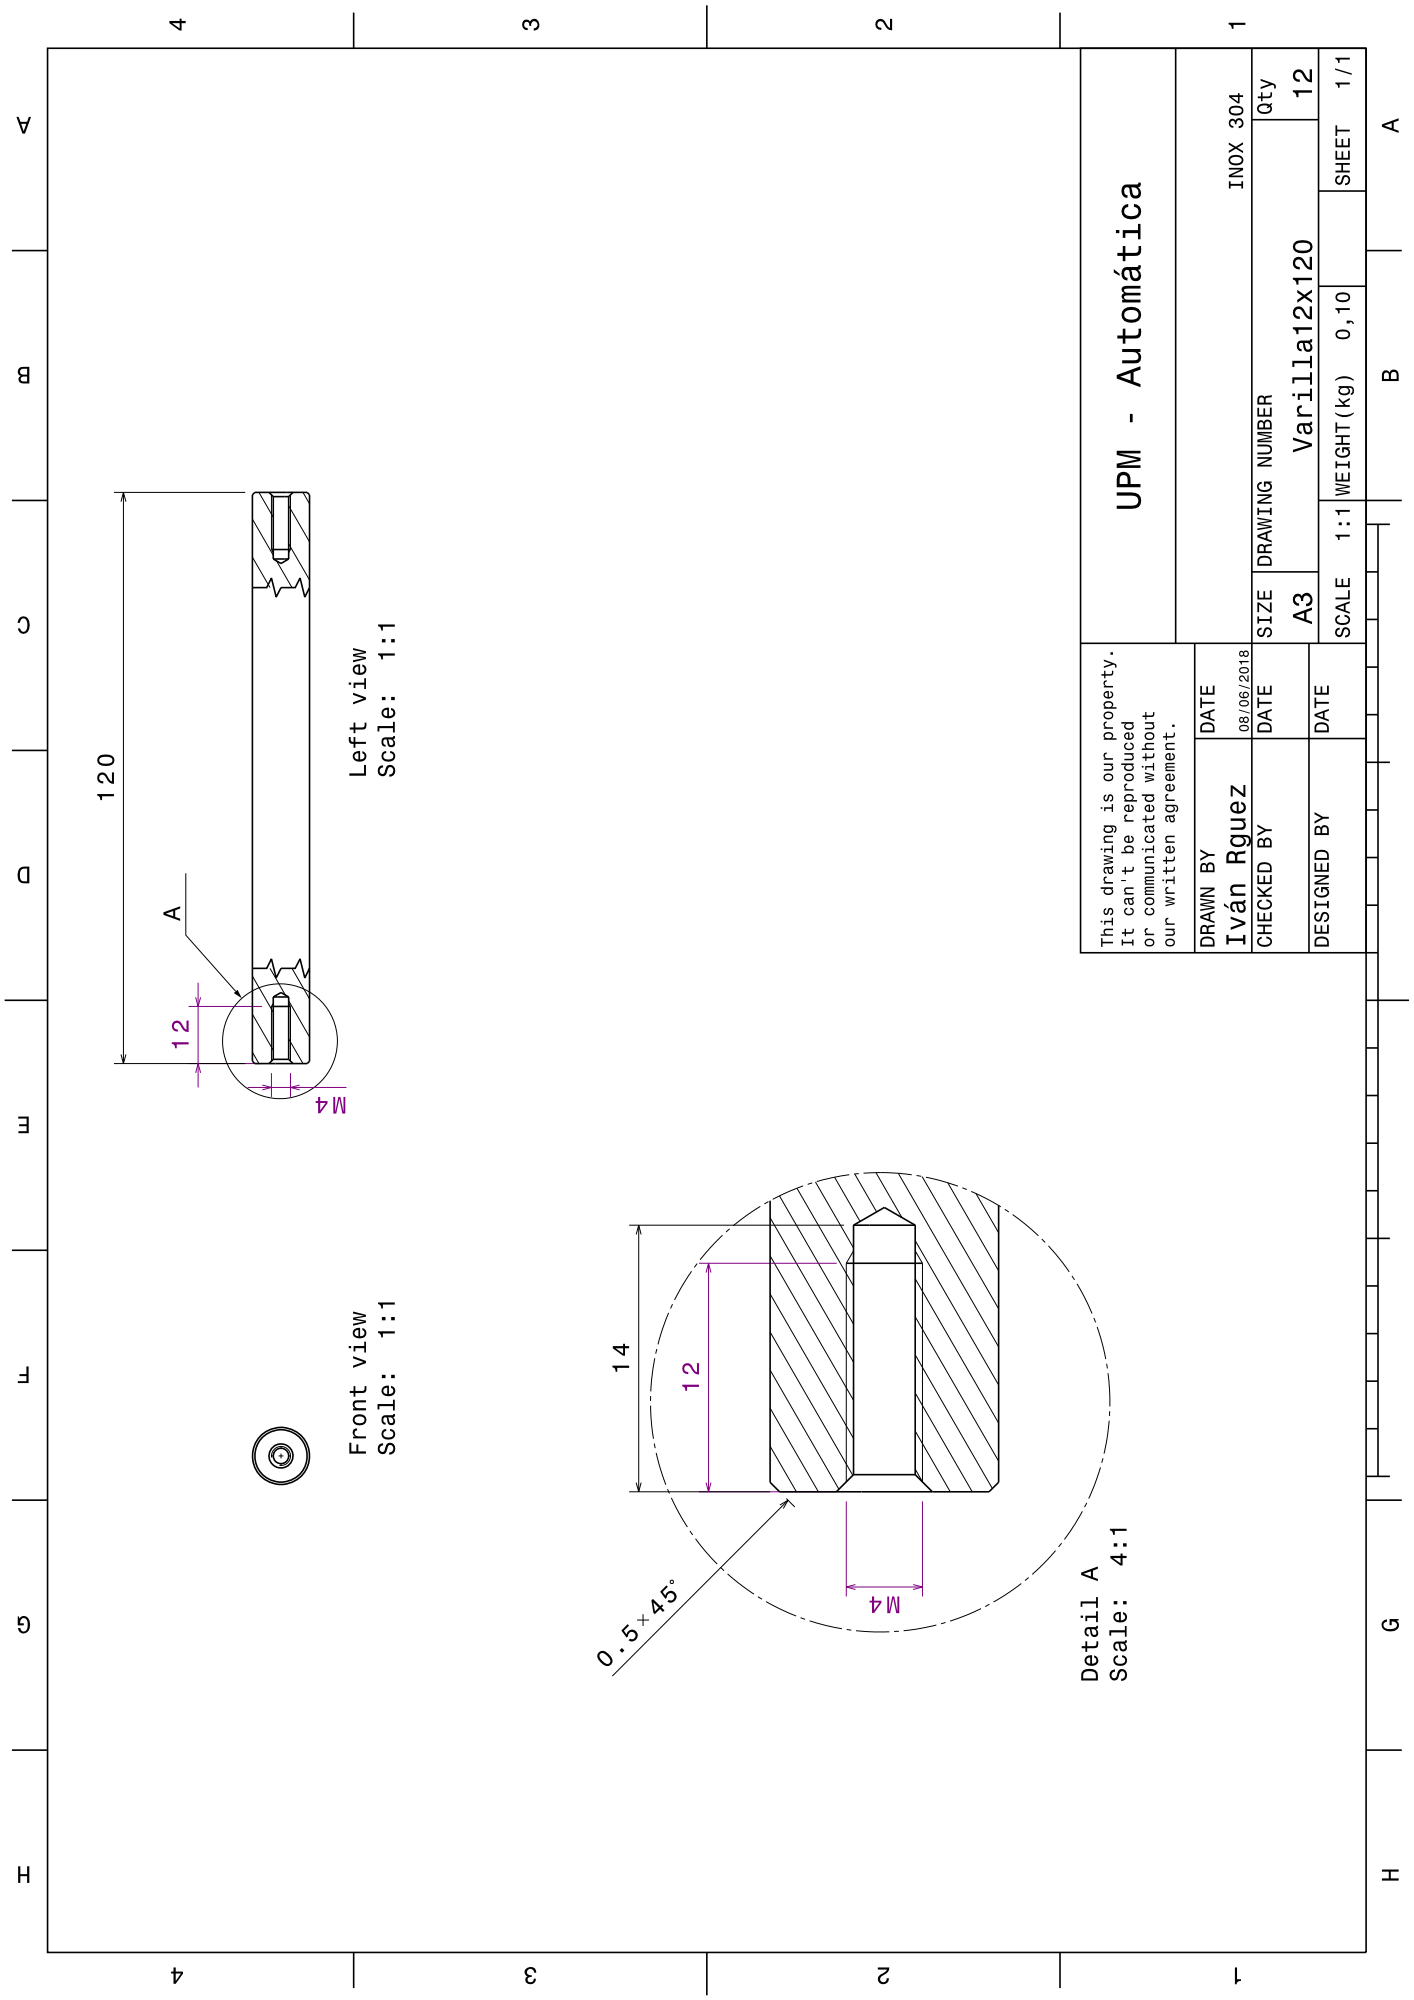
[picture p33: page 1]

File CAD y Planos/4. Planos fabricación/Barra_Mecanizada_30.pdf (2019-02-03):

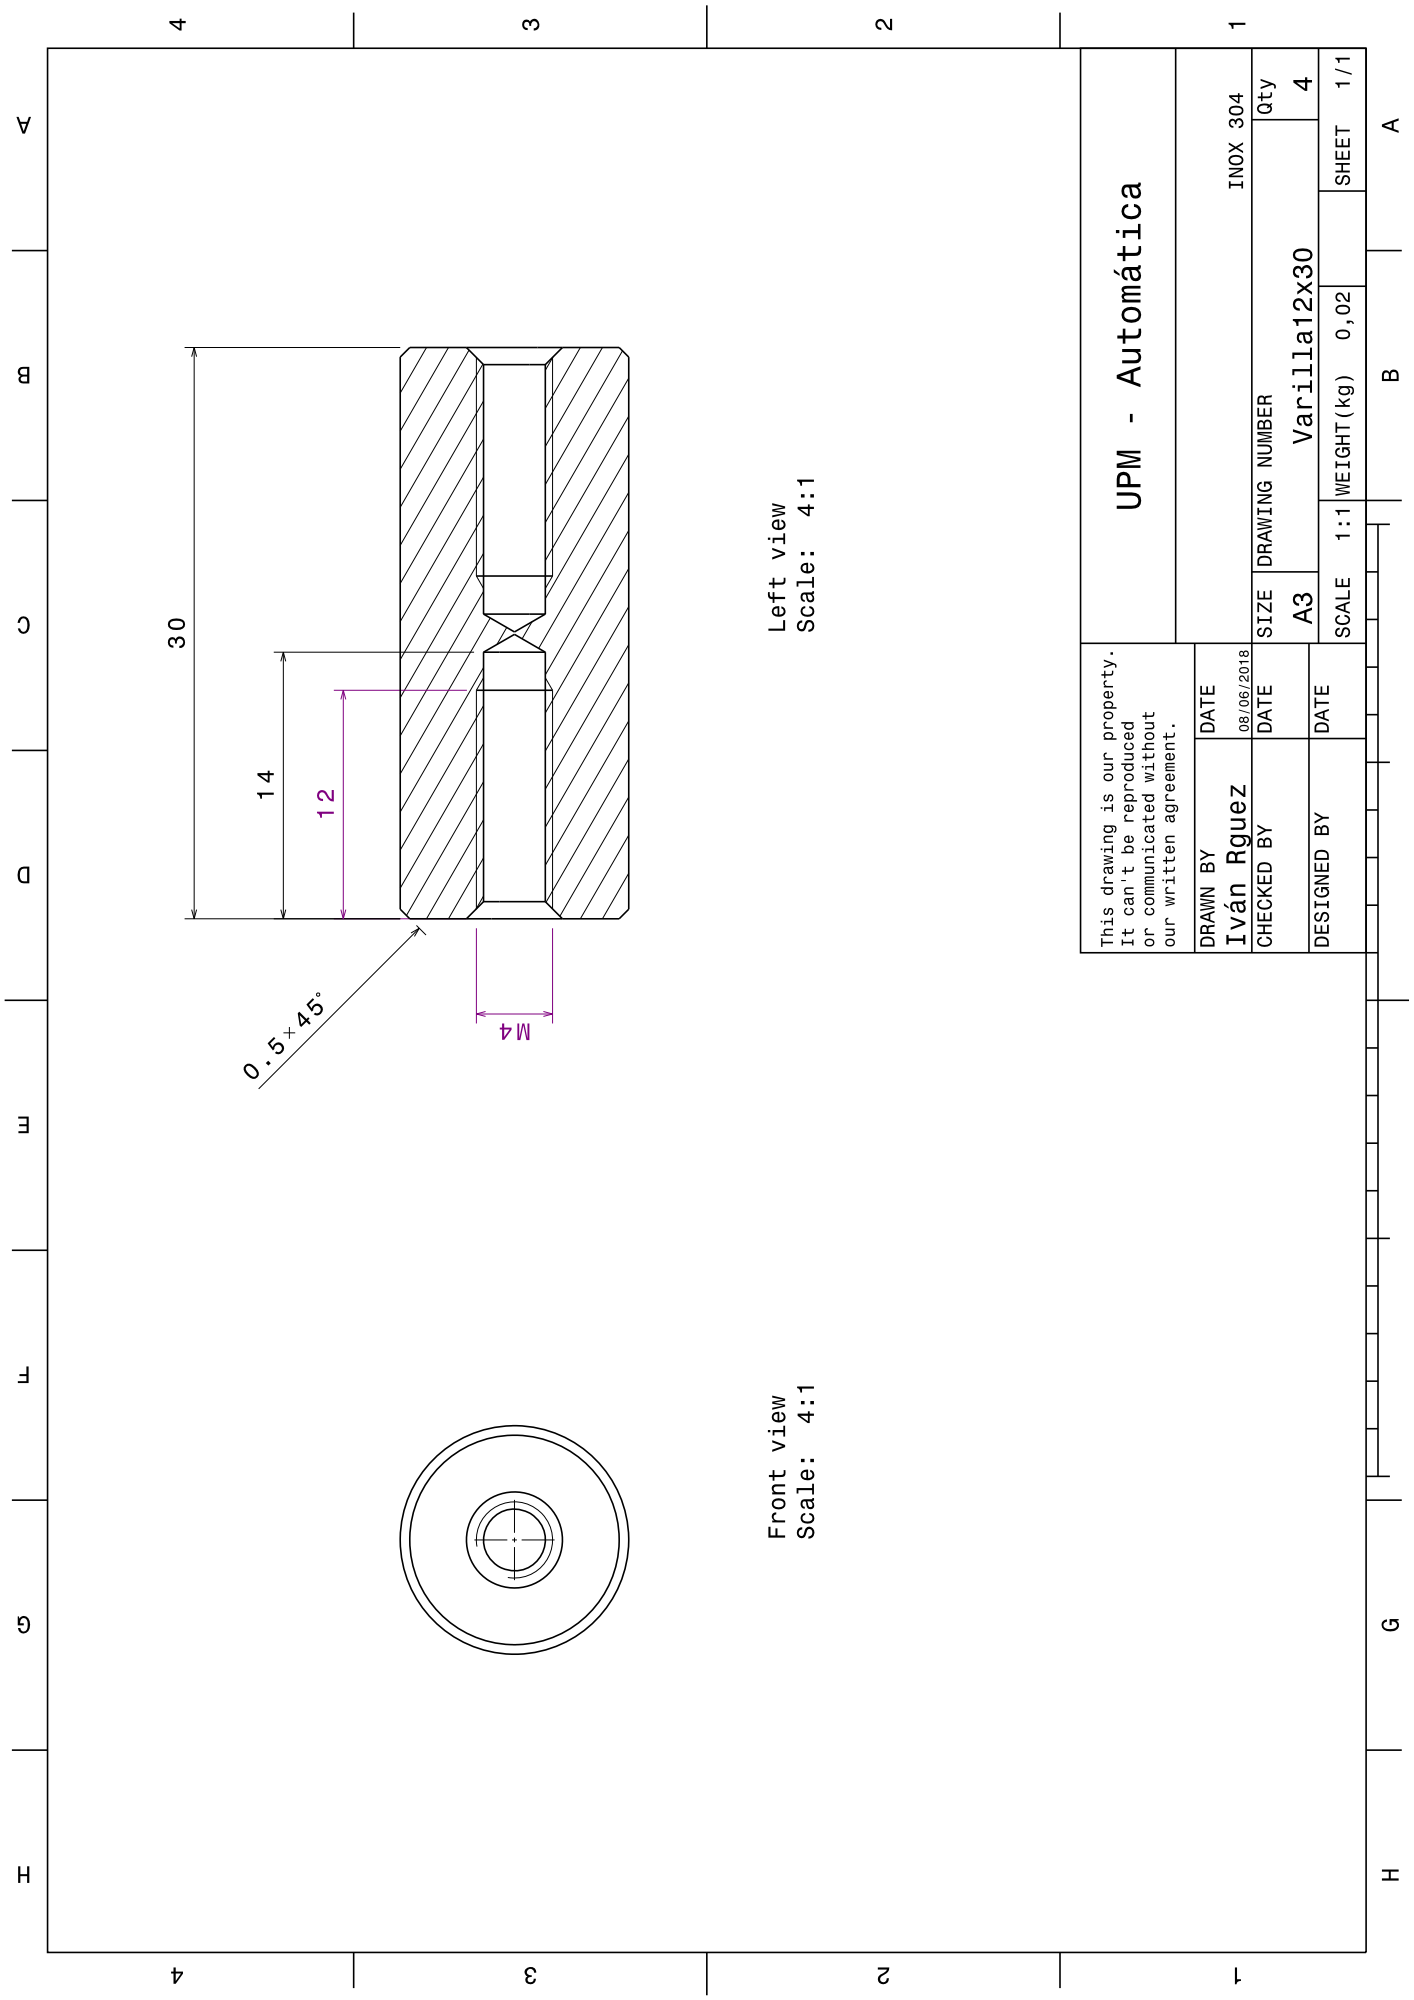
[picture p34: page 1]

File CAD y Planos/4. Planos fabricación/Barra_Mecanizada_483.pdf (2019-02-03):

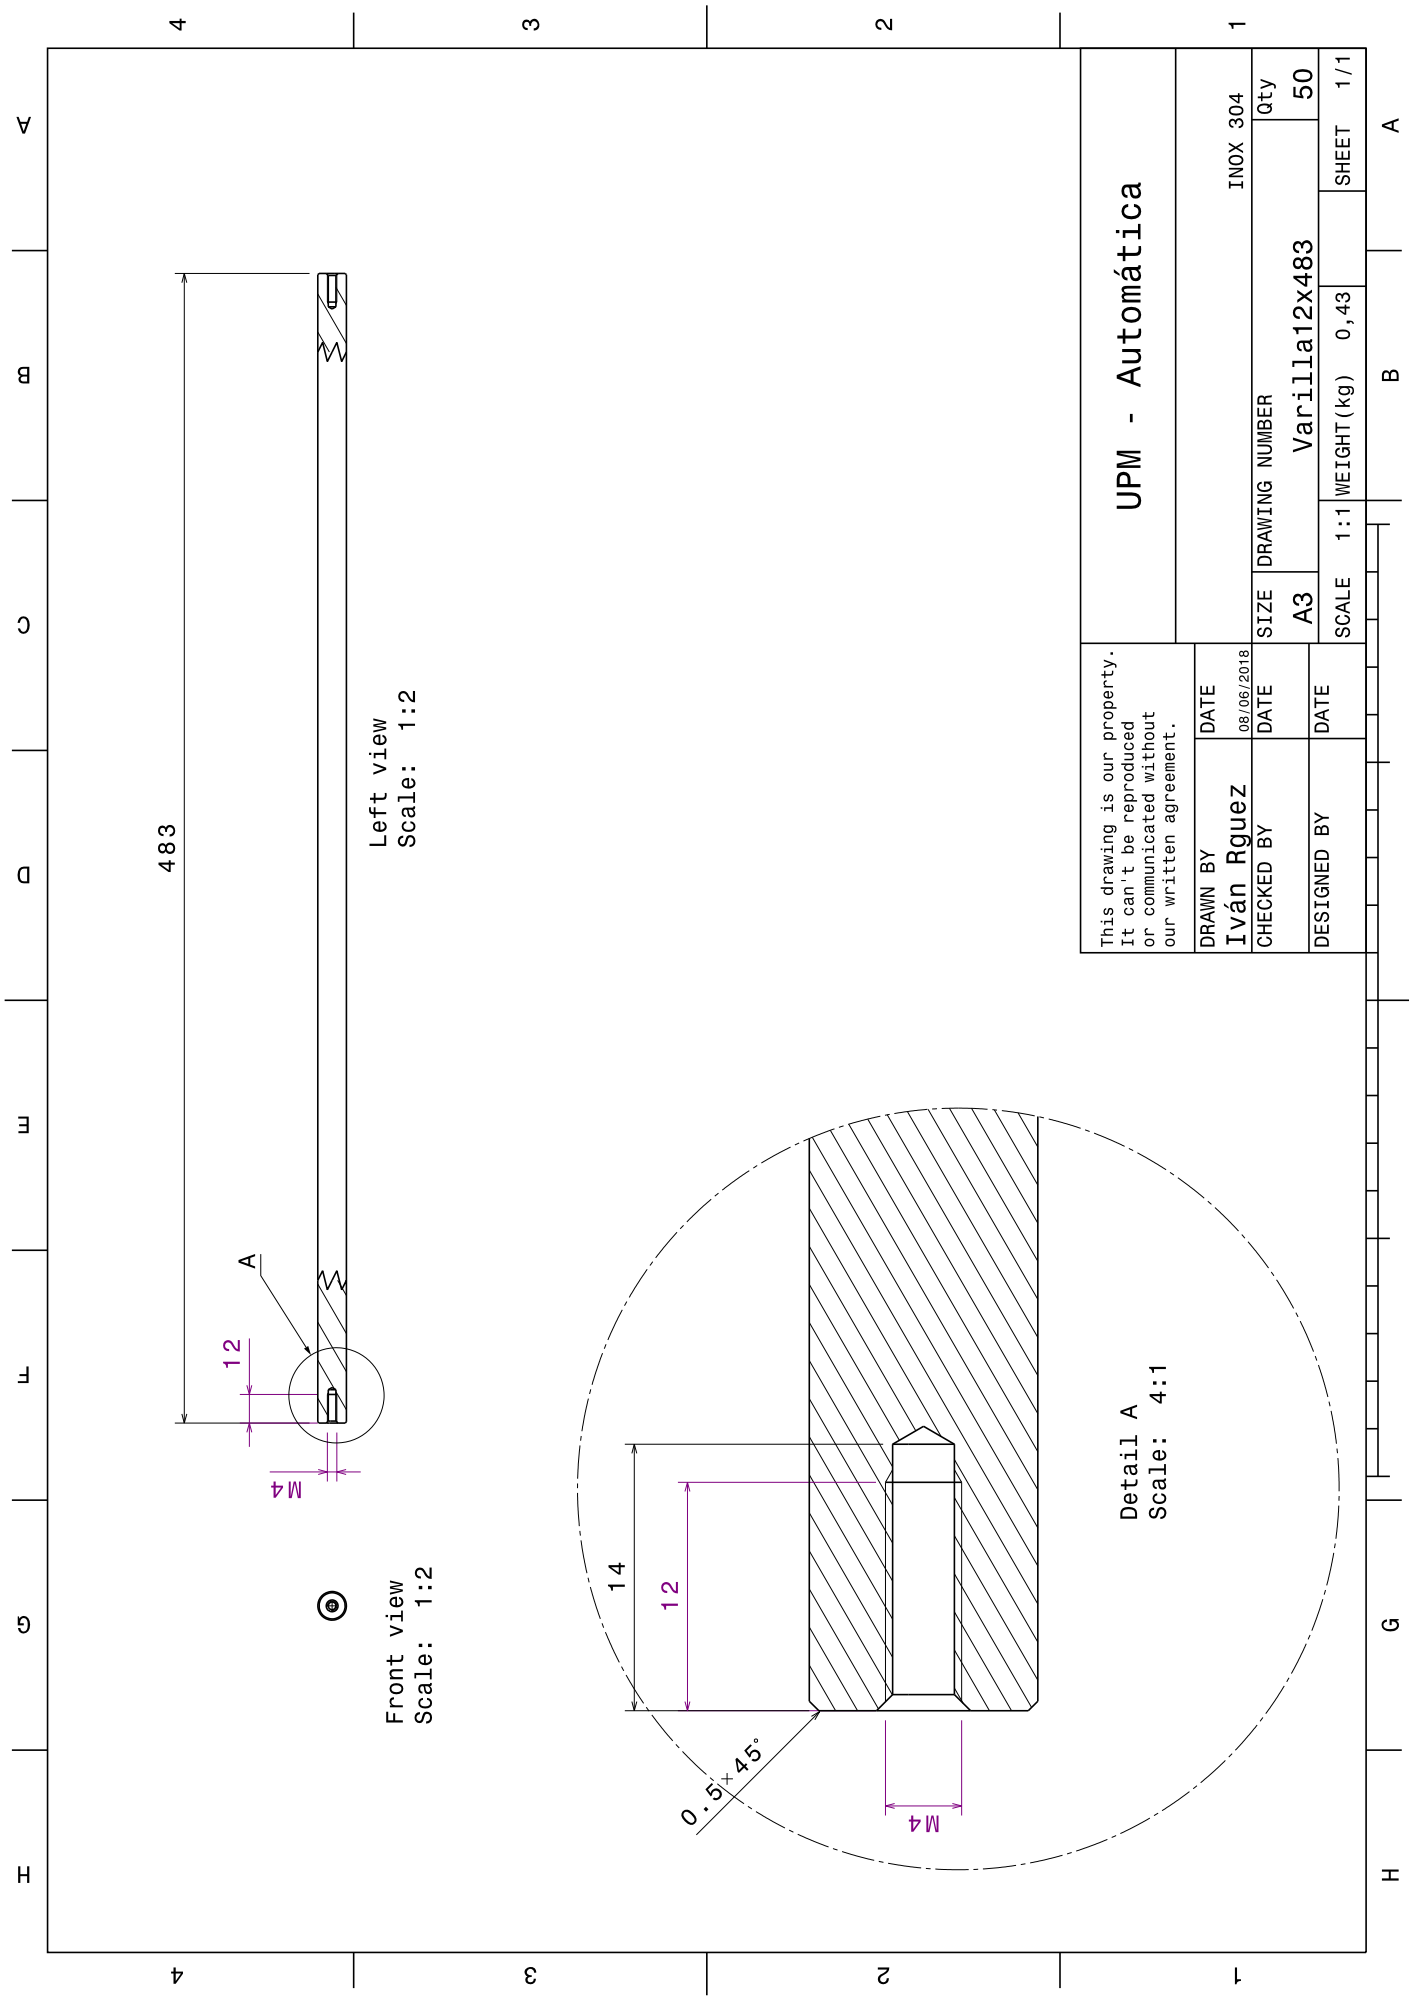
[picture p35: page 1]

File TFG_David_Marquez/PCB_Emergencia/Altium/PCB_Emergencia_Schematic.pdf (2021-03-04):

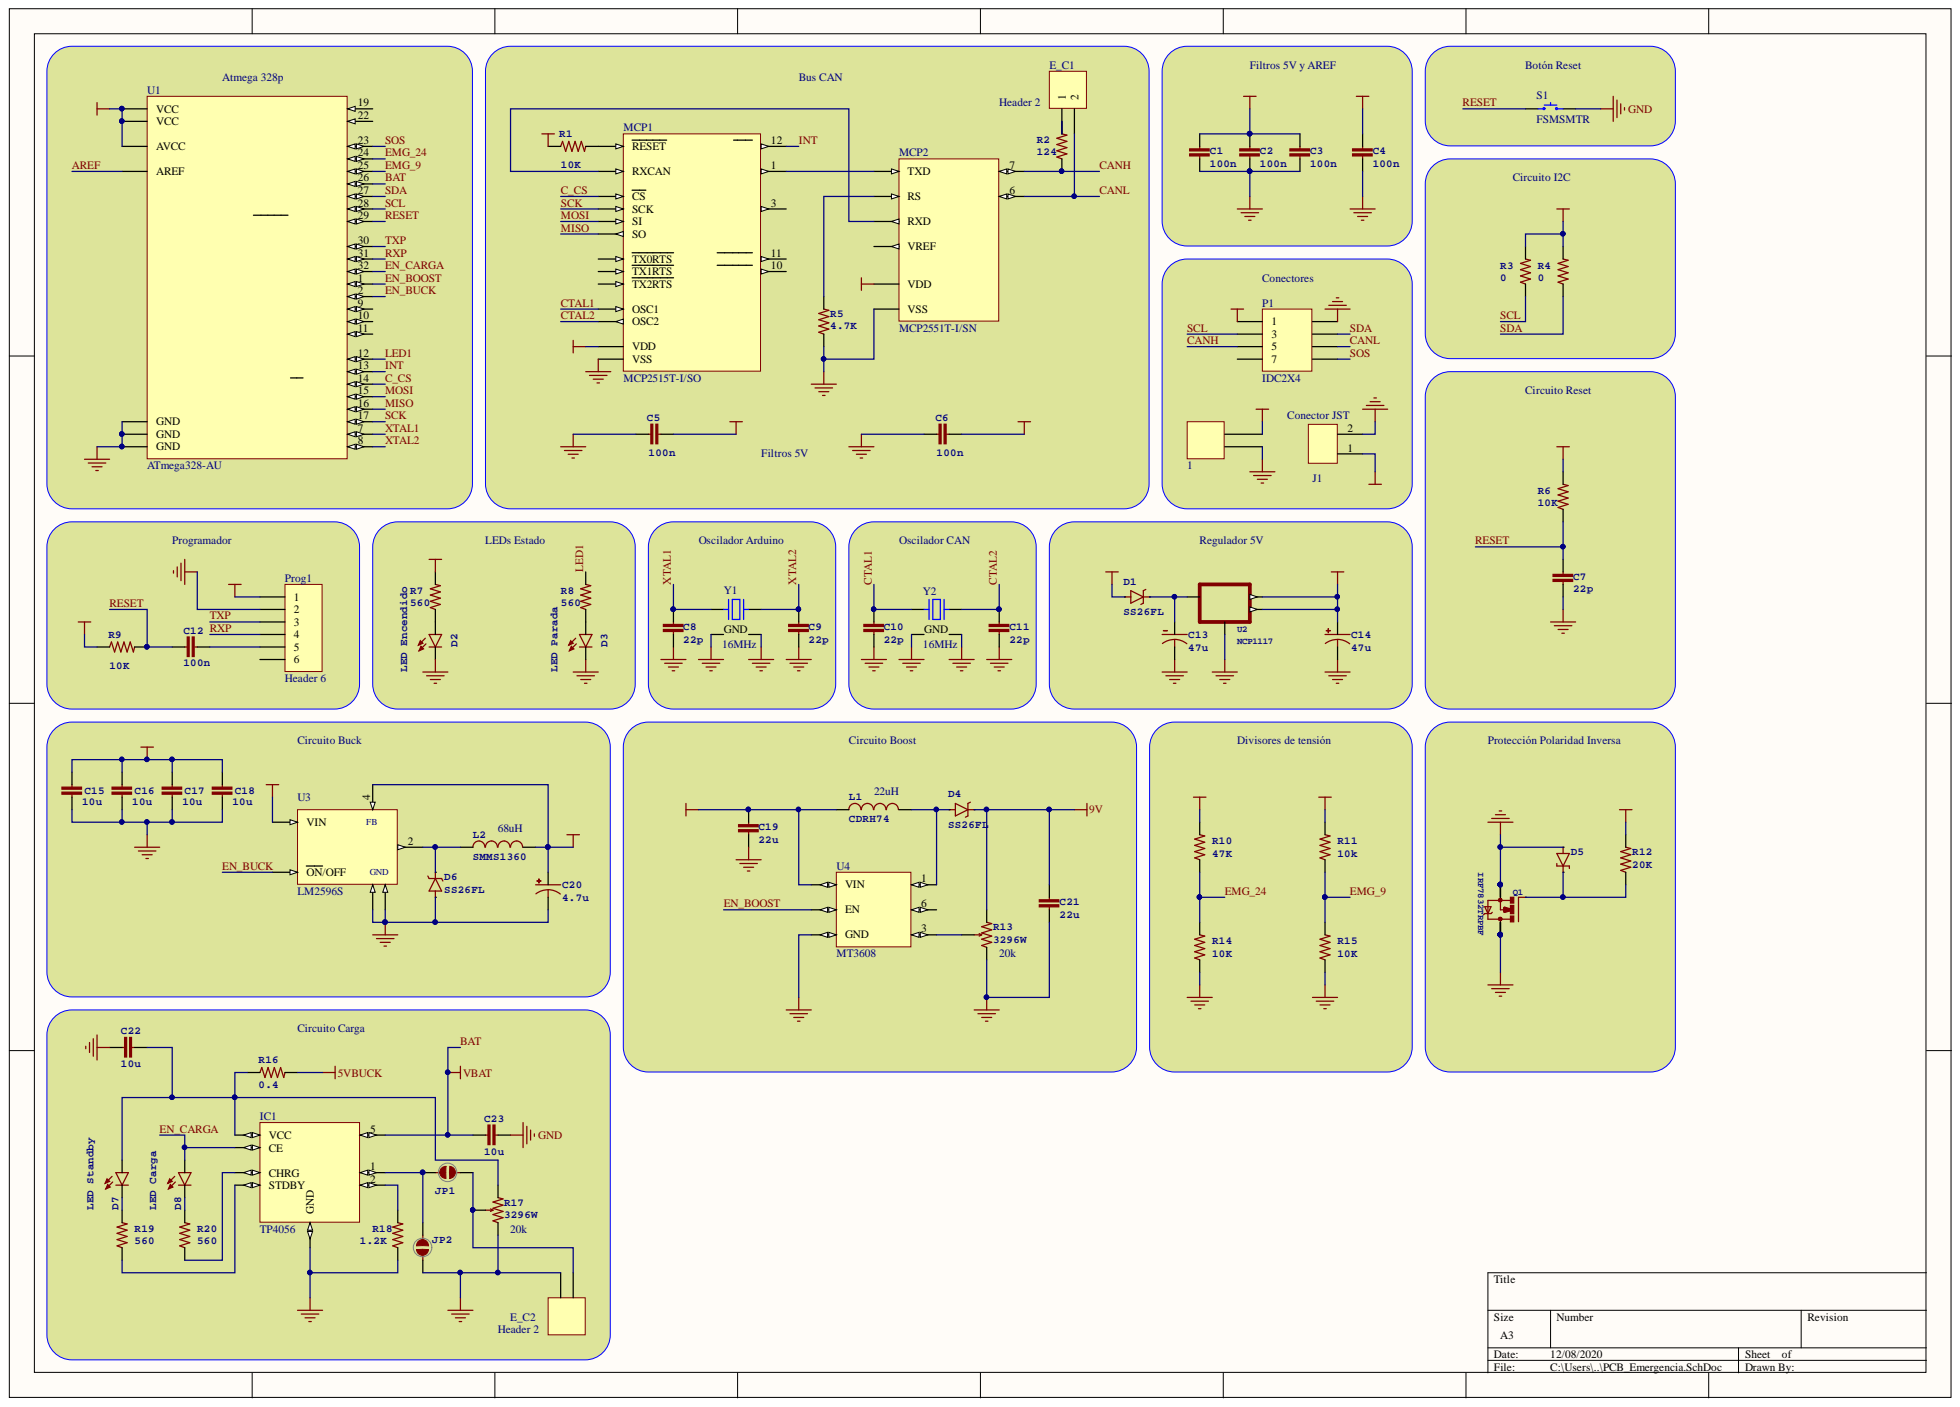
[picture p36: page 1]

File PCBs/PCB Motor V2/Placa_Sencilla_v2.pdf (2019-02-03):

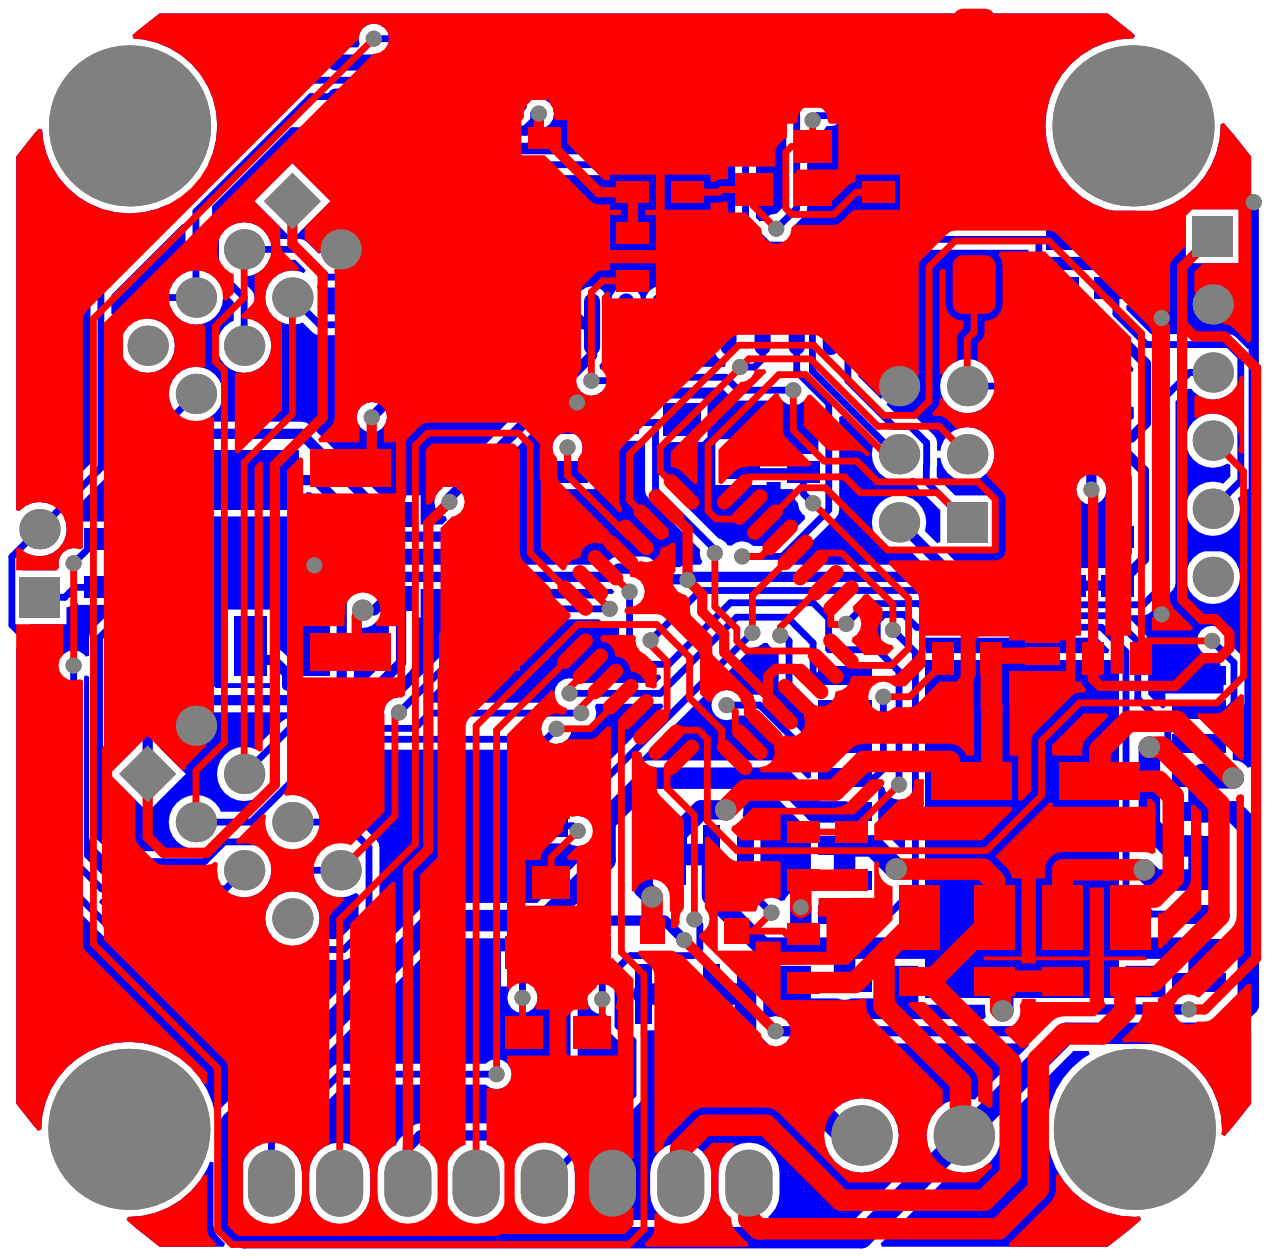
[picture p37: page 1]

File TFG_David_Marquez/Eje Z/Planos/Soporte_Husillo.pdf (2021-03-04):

E | E
F | F

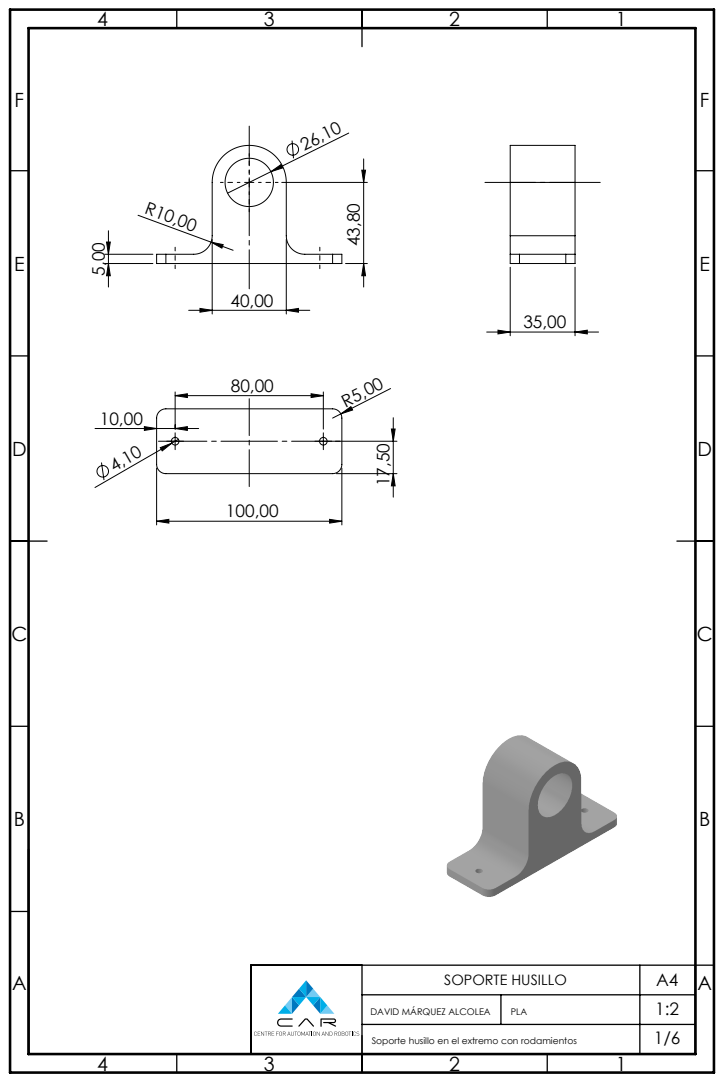
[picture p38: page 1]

SOPORTE HUSILLO | A4

DAVID MÁRQUEZ ALCOLEA | PLA | 1:2

Soporte husillo en el extremo con rodamientos | | 1/6

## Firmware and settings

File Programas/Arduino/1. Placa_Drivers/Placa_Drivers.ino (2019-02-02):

#include <SPI.h>
#include <mcp2515.h>
#include <millis.h> //Utiliza el timer 2
#include <digitalWriteFast.h>
#include <SingleEMAFilterLib.h>



#define ENCODER_OPTIMIZE_INTERRUPTS
#include <Encoder.h>  //44 pulsos por vuelta


//Parametros para la identificacion de placa Driver Unica
#define DriverID 32
#define IDs_per_Driver 50
#define Vel_Samples 5
#define Vel_Sample_Time 5 //ms
#define Dead_Input 20 //Rango PWM a partir del cual tiene efecto en el motor. Aprox 30, default:20
#define Tiempo_Gracia 0.05 //Tiempo que se le deja para que termine de alcanzar la posicion (s)
#define CAN_Tr_Data_Space 8 // Direcciones desde la posicion 1 de la trayectoria hasta la siguiente ej: 0 - 7

#define Max_Puntos_Por_Trayectoria 2

//Opciones Debugger
#define Serial_Debugger 0
#define Serial_Debugger2 0

//Definicion Pines de entrada
#define FS A6
#define FB A7
#define SOS A0
#define End_Stop A1
#define Aux_Input A2
#define ENABLE A3
#define ENC1 2
#define ENC2 3
#define D1 4
#define DRIVER1 5
#define DRIVER2 6
#define D2 7		//Esta negado en el driver
#define LED1 8
#define INT 9
#define C_CS 10


//Definicion Direcciones Bus-CAN utilizadas
	//Direccion del estado de los finales de carrera
#define FDC_ID 2000
#define FDC_LENGTH 5
	//Direccion para peticion de estado finales de carrera
#define UPDATE_REQ_ID 2001
#define UPDATE_REQ_LENGTH 1

//Direcciones Bus-CAN Propias de la placa
#define CAN_Tr_Pos_ID 0
#define CAN_Tr_Pos_Len 4

#define CAN_Tr_Vel_ID 1
#define CAN_Tr_Vel_Len 4

#define CAN_Tr_Acelt_ID 2
#define CAN_Tr_Acelt_Len 4

#define CAN_Tr_Dcelt_ID 3
#define CAN_Tr_Dcelt_Len 4

#define CAN_Tr_Vel_Max_ID 4
#define CAN_Tr_Vel_Max_Len 4

#define CAN_Tr_Time_ID 5
#define CAN_Tr_Time_Len 4

#define CAN_Corriente_ID 41
#define CAN_Corriente_Len 5

#define CAN_Dato_Recv_ID 42
#define CAN_Dato_Recv_Len 1

#define CAN_Pos_Alc_ID 43
#define CAN_Pos_Alc_Len 1

#define CAN_Tr_Env_ID 44
#define CAN_Tr_Env_Len 1

#define CAN_Tr_Recv_ID 45
#define CAN_Tr_Recv_Len 1

#define CAN_Ini_Tr_ID 46
#define CAN_Ini_Tr_Len 1

#define CAN_LED_ID 47
#define CAN_LED_Len 1

#define CAN_Pos_Mot_ID 49
#define CAN_Pos_Mot_Len 4



typedef union   //Guarda el valor en cadena de bytes y luego lo puedo leer en float
{
	float Valor;
	byte Cadena[4];
} FloatUnion;

typedef union
{
	long Valor;
	byte Cadena[4];
} LongUnion;

typedef union
{
	boolean Valor;
	byte Cadena[1];
} BoolUnion;


can_frame ReadMsg;		//Mensaje Reservado para lectura
can_frame WriteMsg;
can_frame UpdateReqFdC;

Encoder Motor_Enc(ENC2, ENC1);

MCP2515 mcp2515(C_CS);   //Pin comunicación SPI Arduino-MCP2515
byte state_FdC[5] = { 0 };
boolean own_FdC = false; //Estado del FdC asociado a la placa

//Definición variable Motor
struct MotorData
{
	long long Pulses_Ant;
	long long t_prev_vel;
	float Vel[Vel_Samples];
	float Vel_F;
};

struct FeedForward
{
	float Input, Output, Kv, Ka;
};

struct PointsData
{
	//Vamos a ver pollito, por BusCAN vamos a recibir solamente Posiciones y Tiempos para esas posiciones
	int Points = 2;
	float MaxSpeed[Max_Puntos_Por_Trayectoria - 1];
	float AcelTime[Max_Puntos_Por_Trayectoria - 1];
	float DcelTime[Max_Puntos_Por_Trayectoria - 1];
	float a, b, c, d, e;
	float Time[Max_Puntos_Por_Trayectoria];
	float Pulses[Max_Puntos_Por_Trayectoria];
	float Speed[Max_Puntos_Por_Trayectoria];
	float Acel[Max_Puntos_Por_Trayectoria];
	float Time_Ini = 0;
};

//Definición variable PIDF
struct PIDData
{
	float Kp, Ki, Kd, Kb, Kn;
	int Sample_time;
	float Error, Proportional, Integral, Derivative, Feedback, Previous_error, Error_WindUp, Derivative_Sum;
	float min_limit, max_limit;
	long long t_act, t_prev;
	long int dt;
	float Input, Output;
	//Para desabilitar el filtro anti Wind-up, igualar Kb a 0 o los limites a 0
};


//Variables Motor
MotorData Motor = { 0 };

//Variables para los PIDs
PIDData PIDVel = { 0 };
PIDData PIDPos = { 0 };
FeedForward FF_1 = { 0 };

//Variables Trayectoria
PointsData Tr_P;	//Definicion de la trayectoria a partir de los puntos recibidos por Bus CAN
					//Para las trayectorias, en pulsos y milisegundos pls
PointsData Tr_1;
PointsData Tr_2;
PointsData Tr_3;


SingleEMAFilter<float> EMAFilter(0.5); //Parametro alfa del filtro
int CAN_Dirs[50] = { 0 };

void setup() {
	//Definicion de los pines de entrada
	//Los encoder se definen dentro de la libreria
	pinMode(FS, INPUT);
	pinMode(FB, INPUT);
	pinMode(SOS, INPUT);
	pinMode(End_Stop, INPUT);
	pinMode(Aux_Input, INPUT);
	pinMode(ENABLE, OUTPUT);
	pinMode(LED1, OUTPUT);
	pinMode(D1, OUTPUT);
	pinMode(DRIVER1, OUTPUT);
	pinMode(DRIVER2, OUTPUT);
	pinMode(D2, OUTPUT);			//Esta negado en el driver
	pinMode(INT, OUTPUT);
	pinMode(C_CS, OUTPUT);

	digitalWrite(ENABLE, LOW);

	TCCR0B = TCCR0B & 0b11111000 | 0x02;	//Los pines 5 y 6 tienen una frecuencia base de 62500Hz, normalmente su divisor es 64, por lo que 
											//la frecuencia asociada al PWM es 976Hz. Con esta funcion se varia el divisor a 8, obteniendo
											//asi una frecuencia de 7812Hz para evitar problemas con la conmutacion de los motores.
											//Esto afecta al timer0, que esta asociado a las funciones de tiempo millis() y delay(), por lo 
											//que sera necesario corregirlo en el codigo en caso de utilizarlas.

	millis_init();			//Inicia la funcion millis alternativa debido a la modificacion del timer0.

	CAN_Dirs_init();
	//Definicion mensajes CAN
	UpdateReqFdC.can_id = UPDATE_REQ_ID;
	UpdateReqFdC.can_dlc = UPDATE_REQ_LENGTH;


	SPI.begin();	//Inicio SPI para comunicacion con el chip Bus-CAN

	while (!Serial);
	Serial.begin(115200);

	mcp2515.reset();
	mcp2515.setBitrate(CAN_125KBPS);
	mcp2515.setNormalMode();
	//mcp2515.setLoopbackMode();

	//Variables Prealimentacion
	FF_1.Ka = 0;
	FF_1.Kv = 1;

	//Variables del PID de velocidad
	PIDVel.Kp = 0.041367;
	PIDVel.Ki = 1.084;			//1.06885687507539;
	PIDVel.Kd = 0.0001;// 0.000074;		//0.055;
	PIDVel.Kb = 1;				//0.108;
	PIDVel.Kn = 76;
	PIDVel.Sample_time = 5;		//ms
	PIDVel.max_limit = 255;
	PIDVel.min_limit = -255;
	PIDVel.Input = 0;			//pulsos/s

	//Variables del PID de Posicion
	PIDPos.Kp = 5.95;// 5.746;
	PIDPos.Ki = 0;//0.65;
	PIDPos.Kd = 0;//0.0625;
	PIDPos.Kn = 100;
	PIDPos.Sample_time = 5;		//ms

	reset_Tr(&Tr_P);

	//Definicion de la trayectoria

	/*
	Tr_P.AcelTime[0] = 0.5;
	Tr_P.DcelTime[0] = 0.5;

	Tr_P.MaxSpeed[0] = 0;
	Tr_P.Time[0] = 0;
	Tr_P.Time[1] = 2;
	Tr_P.Pulses[0] = 0;
	Tr_P.Pulses[1] = 27500; //No sirve para nada, los pulsos se consiguen a partir de la integral.
	Tr_P.Speed[0] = 0;
	Tr_P.Speed[1] = 0;
	Gen_Tr(&Tr_P);

	*/


	/*
	for (float i = Tr_P.Time[0]; i <= Tr_P.Time[1]; i += 0.01) {
		float temp = Tr_Pos(i);
		Serial.print(i);
		for (float j = 0; j <= temp; j += 40) {
			Serial.print("-");
		}
		Serial.print("   ");
		Serial.println(temp);
	}*/



}


int velo = 0;
int incomingByte = 0;   // for incoming serial data
boolean data_logging = false;
int dt = 0; //Diferencia de tiempos con el ultimo muestreo.
int Trayectoria_Iniciada = 0; //Una vez que comienza la trayectoria se pone a 1.
BoolUnion AuxB = { 0 };

void loop() {

	if (Trayectoria_Iniciada) {
		//Calcula la velocidad del motor en funcion de los pulsos de encoder cada Periodo Vel_Sample_Time
		dt = millis_get() - Motor.t_prev_vel;
		if (dt >= Vel_Sample_Time) {
			eval_vel(dt); //Calcula la velocidad de giro a partir de la diferencia de pulsos de encoder.
		}
		//Evalua el PID de posicion cada periodo PIDPos.Sample_time
		PIDPos.dt = millis_get() - PIDPos.t_prev;
		if (PIDPos.dt >= PIDPos.Sample_time) {
			PIDPos.Feedback = Motor_Enc.read();
			PIDPos.Input = Tr_Pos((seconds_get() - Tr_P.Time_Ini)) - PIDPos.Feedback;
			eval_PIDF(&PIDPos);

			Serial_Trayectoria(); //Para imprimir la trayectoria por serial
		}
		//Evalua el PID de velocidad cada Periodo PIDVel.Sample_time
		PIDVel.dt = millis_get() - PIDVel.t_prev;
		if (PIDVel.dt >= PIDVel.Sample_time) {
			eval_FF(&FF_1);//Prealimentacion
			PIDVel.Feedback = Motor.Vel_F;
			PIDVel.Input = PIDPos.Output - PIDVel.Feedback + FF_1.Output; //Entrada al bloque sumador
			eval_PIDF(&PIDVel);
			//Si la salida se encuentra en la zona muerta del motor, se deja en rotacion libre ya que no
			//tendrá ningún efecto.
			if (PIDVel.Output > Dead_Input) { FwMotor((int)PIDVel.Output); }
			else if (PIDVel.Output < -Dead_Input) { RvMotor((int)abs(PIDVel.Output)); }
			else { digitalWrite(ENABLE, LOW); FwMotor(0); }
		}

		if ((seconds_get() - Tr_P.Time_Ini) > (Tr_P.Time[1] + Tiempo_Gracia)) {
			Parar_Tr();// Una vez pasado el tiempo teorico de la trayectoria, se puede dejar un tiempo posterior para que el
			//PID intente llegar a la posicion final en el caso que no la haya alcanzado todavia. Una vez pasado ese tiempo,
			//se detiene la trayectoria.
		}
	}



	//Escucha la direccion CAN de peticiones de estado de los FdC
	if (mcp2515.readMessage(&ReadMsg) == MCP2515::ERROR_OK) {
		if ((ReadMsg.can_id >= CAN_Dirs[0]) && (ReadMsg.can_id <= CAN_Dirs[40])) {//Datos de trayectoria
			Serial.println(ReadMsg.can_id);
			Recibir_Tr();

		}
		else if (ReadMsg.can_id == FDC_ID) { save_FdC(); } //Guarda el estado de FdC en OwnFdC cuando se envia una actualizacion
		else if (ReadMsg.can_id == 1800) {
			Serial.println("Comenzar"); 
			Comenzar_Tr();
		}


		else if (ReadMsg.can_id >= CAN_Dirs[41] && ReadMsg.can_id <= CAN_Dirs[49]) {//Datos Auxiliares
			FloatUnion Aux = { 0 };
			int ID_Aux = ReadMsg.can_id - CAN_Dirs[0]; //Referencia a 0 el ID

			switch (ID_Aux) {
			case CAN_Corriente_ID:
				if (ReadMsg.can_dlc == 1) {
					Aux.Valor = corriente_motor();
					WriteMsg.can_dlc = CAN_Corriente_Len;
					WriteMsg.can_id = (DriverID - 1) * IDs_per_Driver + CAN_Corriente_ID;
					memcpy(WriteMsg.data, Aux.Cadena, WriteMsg.can_dlc);
					while (mcp2515.sendMessage(&WriteMsg)!=0);
				}
				break;
			case CAN_Dato_Recv_ID:
				break;
			case CAN_Pos_Alc_ID:
				break;
			case CAN_Tr_Env_ID:
				//Si me ha terminado de enviar los datos de la trayectoria, la genero.
				Serial.print("Time0: "); Serial.println(Tr_P.Time[0]);
				Serial.print("Time1: "); Serial.println(Tr_P.Time[1]);
				Serial.print("AcelT: "); Serial.println(Tr_P.AcelTime[0]);
				Serial.print("DcelT: "); Serial.println(Tr_P.DcelTime[0]);
				Serial.print("MaxSpeed: "); Serial.println(Tr_P.MaxSpeed[0]);

				Gen_Tr(&Tr_P);

				//Envia el mensaje de que ha recibido la trayectoria :)

				AuxB.Valor = true;
				WriteMsg.can_dlc = 1;
				memcpy(WriteMsg.data, AuxB.Cadena, WriteMsg.can_dlc);
				WriteMsg.can_id = CAN_Tr_Recv_ID;
				while (mcp2515.sendMessage(&WriteMsg)!=0);
				//Hay que comprobar que ha enviado todo y una vez comprobado le decimos que 
				//lo hemos recibido y estamos listos para comenzar

				break;
			case CAN_Tr_Recv_ID:
				break;
			case CAN_Pos_Mot_ID:
				if (ReadMsg.can_dlc == 1) {
					CAN_Update_Pos();
				}
				break;

			case CAN_LED_ID:
				memcpy(AuxB.Cadena, WriteMsg.data, WriteMsg.can_dlc);
				digitalWrite(LED1, AuxB.Valor);
				break;


			default:
				break;
			}
		}
	}

	if (Trayectoria_Iniciada && own_FdC && (Tr_1.Speed[1]<=0)) { //Solo se mueva en direccion contraria al FdC
		Parar_Tr();
	}
}

//---------------------------------------------------------------------
//---------------------------------------------------------------------
//---------------------------------------------------------------------

void CAN_Update_Pos() {
	FloatUnion AuxF = { 0 };
	AuxF.Valor = Motor_Enc.read();
	WriteMsg.can_dlc = CAN_Pos_Mot_Len;
	WriteMsg.can_id = (DriverID - 1) * IDs_per_Driver + CAN_Pos_Mot_ID;
	memcpy(WriteMsg.data, AuxF.Cadena, WriteMsg.can_dlc);
	while(mcp2515.sendMessage(&WriteMsg) != 0);
}
void CAN_Dirs_init() {
	for (int i = 0; i < IDs_per_Driver; i++) {
		CAN_Dirs[i] = (DriverID - 1) * IDs_per_Driver + i;
	}

}
void Comenzar_Tr() {
	if (Trayectoria_Iniciada == 0) {
		reset_PIDF(&PIDPos);
		reset_PIDF(&PIDVel);
		Tr_P.Time_Ini = seconds_get();
		Motor.t_prev_vel = millis_get();
		Motor.Vel_F = 0;
		Motor.Pulses_Ant = Motor_Enc.read();
		Trayectoria_Iniciada = 1;

	}
}

float reset_Tr(struct PointsData *Tr) {
	//Definicion de la trayectoria
	Tr->AcelTime[0] = 0.5;
	Tr->DcelTime[0] = 0.5;
	Tr->MaxSpeed[0] = 0;
	Tr->Time[0] = 0;
	Tr->Time[1] = 0;
	Tr->Pulses[0] = 0; //Motor_Enc.read();
	Tr->Pulses[1] = 0; //No sirve para nada, los pulsos se consiguen a partir de la integral.
	Tr->Speed[0] = 0;
	Tr->Speed[1] = 0;
}

void Parar_Tr() {
	Trayectoria_Iniciada = 0;
	BrakeMotor();
	Serial.println("Parado");
	EMAFilter.ResetValue();
	/*reset_Tr(&Tr_P);
	reset_Tr(&Tr_1);
	reset_Tr(&Tr_2);
	reset_Tr(&Tr_3);*/
}
void Serial_Trayectoria() {
	//Tiempo
	Serial.print((seconds_get() - Tr_P.Time_Ini), 3);
	Serial.print(",\t");
	//Trayectoria Posicion
	Serial.print(Tr_Pos(seconds_get() - Tr_P.Time_Ini));
	Serial.print(",\t");
	//Posicion Real
	Serial.print(Motor_Enc.read());
	Serial.print(",\t");
	//Trayectoria Velocidad
	Serial.print(Tr_Vel(seconds_get() - Tr_P.Time_Ini));
	//Serial.print((int)PIDVel.Output);
	Serial.print(",\t");
	//Trayectoria Velocidad
	Serial.print(Motor.Vel_F);
	Serial.print(",\t");
	//Velocidad
	//Serial.println(Motor.Vel_F);
	Serial.println(PIDVel.Output);
}

void FwMotor(int vel) {
	digitalWrite(ENABLE, HIGH);
	digitalWrite(D1, LOW);
	digitalWrite(D2, HIGH);
	analogWrite(DRIVER1, vel);
	digitalWrite(DRIVER2, LOW);
}

void RvMotor(int vel) {
	digitalWrite(ENABLE, HIGH);
	digitalWrite(D1, LOW);
	digitalWrite(D2, HIGH);
	analogWrite(DRIVER2, vel);
	digitalWrite(DRIVER1, LOW);
}

void BrakeMotor() {
	digitalWrite(ENABLE, HIGH);
	digitalWrite(D1, LOW);
	digitalWrite(D2, HIGH);
	analogWrite(DRIVER1, LOW);
	digitalWrite(DRIVER2, LOW);
}


void prntBits(int b)
{
	for (int i = 7; i >= 0; i--)
	{
		Serial.print(bitRead(b, i));
	}
	Serial.println("");
}

void save_FdC() {
	memcpy(state_FdC, ReadMsg.data, ReadMsg.can_dlc); //Copia ReadMsg.data en State_FdC
	//Compara si el FdC pulsado corresponde a esta placa
	if ((state_FdC[(DriverID - 1) / 8] & (0b00000001 << (DriverID - 1) % 8)) != 0)
	{
		own_FdC = true; //Se recibe el mensaje con los estados de los FdC, si el resultado
						//es positivo significa que el FdC de esta placa está pulsado.
	}
	else { own_FdC = false; }
}


void Recibir_Tr() {
	FloatUnion Aux = { 0 };
	memcpy(Aux.Cadena, ReadMsg.data, ReadMsg.can_dlc);
	//Ya sabemos que los ID's son de trayectoria y corresponden a esta placa, 
	//por lo que lo referenciamos a 0 para facilitar el manejo
	int ID_Aux = ReadMsg.can_id - CAN_Dirs[0];

	switch (ID_Aux % CAN_Tr_Data_Space)
	{
	case 0:
		Tr_P.Pulses[ID_Aux / (int)CAN_Tr_Data_Space] = Aux.Valor;
		break;
	case 1:
		Tr_P.Speed[ID_Aux / (int)CAN_Tr_Data_Space] = Aux.Valor;
		break;
	case 2:
		Tr_P.AcelTime[ID_Aux / (int)CAN_Tr_Data_Space] = Aux.Valor;
		break;
	case 3:
		Tr_P.DcelTime[ID_Aux / (int)CAN_Tr_Data_Space] = Aux.Valor;
		break;
	case 4:
		Tr_P.MaxSpeed[ID_Aux / (int)CAN_Tr_Data_Space] = Aux.Valor;
		break;
	case 5:
		Tr_P.Time[ID_Aux / (int)CAN_Tr_Data_Space] = Aux.Valor;
		//Serial.println(ID_Aux / (int)CAN_Tr_Data_Space);
	default:
		break;
	}
	//Definicion de la trayectoria
	/*Tr_P.AcelTime[0] = 0.5;
	Tr_P.DcelTime[0] = 0.5;

	Tr_P.MaxSpeed[0] = 0;
	Tr_P.Time[1] = 1;
	Tr_P.Pulses[0] = 0;
	Tr_P.Pulses[1] = 27500; //No sirve para nada, los pulsos se consiguen a partir de la integral.
	Tr_P.Speed[0] = 0;
	Tr_P.Speed[1] = 0;
	Gen_Tr(&Tr_P);*/
}

float corriente_motor() {
	return analogRead(FB)*(5.0 / 1024.0)*(375.0 / 200.0);	//El Driver MC33887 tiene feedback de corriente,
															//la cual es leida con esta funcion.
}

void delay_mod(long tiempo) {
	volatile long long t_init = millis_get();
	while (millis_get() - t_init < tiempo) {}
}


void eval_vel(float dt) {
	//EMAFilter.AddValue() devuelve directamente el valor filtrado LP.
	//Se multiplica por 1000 para obtener pulsos/s, ya que dt viene dado en ms.
	Motor.Vel_F = EMAFilter.AddValue(1000 * (Motor_Enc.read() - Motor.Pulses_Ant) / (float)dt);
	Motor.Pulses_Ant = Motor_Enc.read();
	Motor.t_prev_vel = millis_get();
}

void eval_FF(struct FeedForward *FF) {
	FF->Output = FF->Kv * Tr_Vel(seconds_get() - Tr_P.Time_Ini) +
		FF->Ka*Tr_Acel(seconds_get() - Tr_P.Time_Ini);
}


void eval_PIDF(struct PIDData *PID) {
	//Cuidadoooooo, hay que mirar que hacer con T_prev, se va a la puta cuando sale del pid
	PID->t_act = millis_get();
	PID->dt = PID->t_act - PID->t_prev;
	PID->Error = PID->Input;
	PID->Proportional = PID->Error*PID->Kp;
	PID->Integral += (PID->Error*PID->Ki + PID->Kb*PID->Error_WindUp)*0.001*PID->dt;

	if (abs(PID->Error - PID->Previous_error) > 0.01) { //Evitar cociente 0/0
		if (PID->Kn > 0) { //Filtro derivativo
			PID->Derivative_Sum += PID->Derivative*0.001*PID->dt;
			PID->Derivative = ((PID->Error*PID->Kd) - PID->Derivative_Sum)*PID->Kn;
		}
		else {
			PID->Derivative = PID->Error * (PID->Error - PID->Previous_error) / (float)(0.001*PID->dt);
		}
	}
	else { PID->Derivative = 0; }

	PID->Output = PID->Proportional + PID->Integral + PID->Derivative;

	PID->t_prev = PID->t_act;
	PID->Previous_error = PID->Error;

	if (PID->max_limit != 0 || PID->min_limit != 0) {
		PID->Error_WindUp = PID->Output;
		if (PID->Output > PID->max_limit) {
			PID->Output = PID->max_limit;
		}
		else if (PID->Output < PID->min_limit) {
			PID->Output = PID->min_limit;
		}
		PID->Error_WindUp = PID->Output - PID->Error_WindUp;  //Filtro WindUp
	}
}

void reset_PIDF(struct PIDData *PID) {
	PID->Error = 0;
	PID->Proportional = 0;
	PID->Integral = 0;
	PID->Derivative = 0;
	PID->Previous_error = 0;
	PID->Error_WindUp = 0;
	PID->Derivative_Sum = 0;
	PID->t_act = 0;
	PID->t_prev = millis_get();
	PID->Output = 0;
	PID->dt = 0;
	PID->Input = 0;
}
float Gen_Tr(struct PointsData *Tr) {
	Tr_1.Time[0] = Tr->Time[0];
	Tr_1.Time[1] = Tr->Time[0] + Tr->AcelTime[0];
	Tr_1.Speed[0] = Tr->Speed[0];
	Tr_1.Speed[1] = Tr->MaxSpeed[0];
	Tr_1.Acel[0] = 0;
	Tr_1.Acel[1] = 0;
	Tr_1.Pulses[0] = Tr->Pulses[0];
	Calcular_Coef(&Tr_1);
	Tr_1.Pulses[1] = Tr_Pos(Tr_1.Time[1]);

	Tr_2.Time[0] = Tr_1.Time[1];
	Tr_2.Time[1] = Tr->Time[1] - Tr->DcelTime[0];
	Tr_2.Speed[0] = Tr->MaxSpeed[0];
	Tr_2.Speed[1] = Tr->MaxSpeed[0];
	Tr_2.Pulses[0] = Tr_1.Pulses[1];
	Calcular_Coef(&Tr_2);
	Tr_2.Pulses[1] = Tr_Pos(Tr_2.Time[1]);

	Tr_3.Points = 2;
	Tr_3.Time[0] = Tr_2.Time[1];
	Tr_3.Time[1] = Tr->Time[1];
	Tr_3.Speed[0] = Tr->MaxSpeed[0];
	Tr_3.Speed[1] = Tr->Speed[1];
	Tr_3.Acel[0] = 0;
	Tr_3.Acel[1] = 0;
	Tr_3.Pulses[0] = Tr_2.Pulses[1];
	Calcular_Coef(&Tr_3);
	Tr_3.Pulses[1] = Tr_Pos(Tr_3.Time[1]);

}
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

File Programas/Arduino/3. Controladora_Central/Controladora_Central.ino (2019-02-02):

#include <SPI.h>
#include <mcp2515.h>
#include <SingleEMAFilterLib.h>

//Parametros para la identificacion de placa Driver Unica
#define IDs_per_Driver 50	
#define Motors_Number 36	//Numero de motores maximos en el actuador
#define Inst_Mot 24			//Numero de motores instalados en el actuador
#define Config_Lines 10		//Numero de lineas reservadas para la configuracion
#define CAN_Tr_Data_Space 8 // Direcciones desde la posicion 1 de la trayectoria hasta la siguiente ej: 0 - 7

#define Max_Puntos_Por_Trayectoria 2

//Definicion Pines de entrada

#define SOS 32
#define INT 33
#define MISO 50
#define MOSI 51
#define SCK 52
#define C_CS 53

#define LED1 11
#define LED2 12
#define LED3 13

#define BT_STATE 4
#define BT_RX 5
#define BT_TX 6
#define BT_EN 7

#define SDA 20
#define SCL 21

#define Aux_1 A3
#define Aux_2 A2
#define Aux_3 A1
#define Aux_4 A0
#define Aux_5 3
#define Aux_6 2
#define Aux_7 9
#define Aux_8 8
#define Aux_9 23
#define Aux_10 24
#define Aux_11 25
#define Aux_12 26
#define Aux_13 27
#define Aux_14 28
#define Aux_15 29
#define Aux_16 30



//Definicion Direcciones Bus-CAN utilizadas
	//Direccion del estado de los finales de carrera
#define FDC_ID 2000
#define FDC_LENGTH 5
	//Direccion para peticion de estado finales de carrera
#define UPDATE_REQ_ID 2001
#define UPDATE_REQ_LENGTH 1

//Direcciones Bus-CAN Propias de la placa
#define CAN_Tr_Pos_ID 0
#define CAN_Tr_Pos_Len 4

#define CAN_Tr_Vel_ID 1
#define CAN_Tr_Vel_Len 4

#define CAN_Tr_Acelt_ID 2
#define CAN_Tr_Acelt_Len 4

#define CAN_Tr_Dcelt_ID 3
#define CAN_Tr_Dcelt_Len 4

#define CAN_Tr_Vel_Max_ID 4
#define CAN_Tr_Vel_Max_Len 4

#define CAN_Tr_Time_ID 5
#define CAN_Tr_Time_Len 4

#define CAN_Corriente_ID 41
#define CAN_Corriente_Len 5

#define CAN_Dato_Recv_ID 42
#define CAN_Dato_Recv_Len 1

#define CAN_Pos_Alc_ID 43
#define CAN_Pos_Alc_Len 1

#define CAN_Tr_Env_ID 44
#define CAN_Tr_Env_Len 1

#define CAN_Tr_Recv_ID 45
#define CAN_Tr_Recv_Len 1

#define CAN_Ini_Tr_ID 46
#define CAN_Ini_Tr_Len 1

#define CAN_Pos_Mot_ID 49
#define CAN_Pos_Mot_Len 4



typedef union
{
	float Valor;
	byte Cadena[4];
} FloatUnion;

typedef union
{
	long Valor;
	byte Cadena[4];
} LongUnion;

typedef union
{
	boolean Valor;
	byte Cadena[1];
} BoolUnion;


can_frame ReadMsg;		//Mensaje Reservado para lectura
can_frame WriteMsg;


MCP2515 mcp2515(C_CS);
byte state_FdC[5] = { 0 };
boolean own_FdC = false; //Estado del FdC asociado a la placa



struct PointsData
{
	//Vamos a ver pollito, por BusCAN vamos a recibir solamente Posiciones y Tiempos para esas posiciones
	int Points = 2;
	float MaxSpeed[Max_Puntos_Por_Trayectoria - 1];
	float AcelTime[Max_Puntos_Por_Trayectoria - 1];
	float DcelTime[Max_Puntos_Por_Trayectoria - 1];
	float a, b, c, d, e;
	float Time[Max_Puntos_Por_Trayectoria];
	float Pulses[Max_Puntos_Por_Trayectoria];
	float Speed[Max_Puntos_Por_Trayectoria];
	float Acel[Max_Puntos_Por_Trayectoria];
	float Time_Ini = 0;
};



//Variables Trayectoria
PointsData Tr_P;	//Definicion de la trayectoria a partir de los puntos recibidos por Bus CAN
					//Para las trayectorias, en pulsos y milisegundos pls


boolean Tr_Recibida[Motors_Number] = { false };
int Suma_Tr_Recibida = 0;
boolean Pos_Alcanzada[Motors_Number] = { false };
float Pos_Motor[Motors_Number] = { 0 }; //Posicion del motor en pulsos de encoder.
boolean Pos_Recibidas_m[Motors_Number] = { false }; //Numero del motor del cual se han recibido las posiciones.
int Pos_Recibidas = 0; //Numero de Posiciones que se han recibido, en teoria hasta 24.
float Pos_Motor_Destino[Motors_Number] = { 0 };
float Vel_Motor_Max[Motors_Number] = { 0 };
float Pos_Diferencia[Motors_Number] = { 0 };
float Configuracion[Config_Lines] = { 0 }; //Vmax, AcelTime, DcelTime, Time...
float Reductora_Motor[Motors_Number] = { 51,27,0,27,27, 0,51,27,0,27, 27,0,51,27,0, 27,27,0,51,27, 0,27,27,0,51,
										 27,0,27,27,0, 51,27,0,27,27, 0 };		//3,6,9,12,15,18,21,24,27,30,33,36
int Mot_I[Inst_Mot] = { 1,2,4,5,7,8,10,11,13,14,16,17,19,20,22,23,25,26,28,29,31,32,34,35 };

void setup() {
	//Definicion de los pines de entrada
	//Los encoder se definen dentro de la libreria
	pinMode(SOS, INPUT);
	pinMode(LED1, OUTPUT);
	pinMode(LED2, OUTPUT);
	pinMode(LED3, OUTPUT);
	pinMode(INT, OUTPUT);
	pinMode(C_CS, OUTPUT);


	Serial.begin(115200);
	while (Serial.available()) { Serial.read(); }
	Serial.setTimeout(200);

	//Iniciar Bus-CAN
	SPI.begin();	//Inicio SPI para comunicacion con el chip Bus-CAN
	mcp2515.reset();
	mcp2515.setBitrate(CAN_125KBPS);
	mcp2515.setNormalMode();

	//Configuracion por defecto
	Configuracion[0] = 1000;//Vmax
	Configuracion[1] = 0.5;//AcelTime
	Configuracion[2] = 0.5;//DecelTime
	Configuracion[3] = 0;//Time
}


int incomingByte = 0;   // for incoming serial data
boolean data_logging = false;
int dt = 0; //Diferencia de tiempos con el ultimo muestreo.
int Trayectoria_Iniciada = 0; //Una vez que comienza la trayectoria se pone a 1.
long tant = 0;
char S_Byte;
char buffer[16];
int size = -1;

void loop() {
	if (millis() - tant >= 1000) {
		tant = millis();
		//Temporizador
	}


	//Escucha Serial Matlab
	if (Serial.available() > 0) {

		memset(buffer, 0, sizeof(buffer)); //Se vacia el buffer
		size = Serial.readBytesUntil('\n', buffer, 16); //Se lee la linea de encabezado, a ver que es

		//Rececpcion de las trayectorias de los motores (Vmax)
		if (strcmp(buffer, "#Tr_1") == 0) {
			Rec_Vel_Max();
			for (int i = 0; i < Inst_Mot; ++i)
			{
				Gen_Tr_Msg(&Tr_P, Mot_I[i]);
				Enviar_Tr(&Tr_P, Mot_I[i]);
				Read_BusCAN();
			}
			long long Tant_aux = millis();
			while (Suma_Tr_Recibida < 24) {
				Read_BusCAN();
				if (millis() - Tant_aux >= 2000) {

					Serial.println(Suma_Tr_Recibida); break;
				}
			}
			if (Suma_Tr_Recibida == 24) { Serial.println("OK"); }
			Suma_Tr_Recibida = 0;

		}

		//Recepcion de la señal para comenzar el movimiento.
		if (strcmp(buffer, "#Ini") == 0) {
			Iniciar_Movimientos();
		}

		//Peticion para enviar las posiciones actuales de los motores.
		if (strcmp(buffer, "#Pos") == 0) {
			Update_Posicion_Motor(0); //Si el valor de entrada es 0 actualiza todos, en caso de ser diferente actualiza el valor introducido.
			for (int i = 0; i < Inst_Mot; ++i) {
				Serial.println(Pos_Motor[Mot_I[i] - 1]);
			}
			//memset(Pos_Motor, 0, sizeof(Pos_Motor));
			//Control de errores
			Serial.println("Errors");
			Serial.println(Inst_Mot - Pos_Recibidas);
			//Identificacion de placas problematicas
			if (Inst_Mot - Pos_Recibidas > 0) {
				boolean AuxSerial = false;
				for (int i = 0; i < Inst_Mot; i++) {
					if (Pos_Recibidas_m[Mot_I[i] - 1] != true) {
						if (AuxSerial) { Serial.print(" - "); }
						Serial.print(Mot_I[i]);
						AuxSerial = true;
					}
				}
				Serial.print('\n');
			}
			memset(Pos_Recibidas_m, 0, sizeof(Pos_Recibidas_m));
		}

		//Recepcion de la configuracion global de todas las trayectorias.
		if (strcmp(buffer, "#Conf_1") == 0) {
			Rec_Config();
		}
	}

	//Escucha Bus-CAN
	Read_BusCAN();
}
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

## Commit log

2019-02-02 Programas Arduino
2019-02-02 CAD Update Step
    [0. Robot_Completo.CATProduct, 0.Base_Completa.CATProduct, 10pcs_4mm_St_Soporte_Cardan.dxf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]
2021-03-04 TFG DMA
    Primer commit. Sin simulador.
    [3296W.PcbLib, 3296W.SchLib, 6000-Bearing.SLDPRT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]
2021-03-05 Unity 0.1
    Sin simulación
    [Armario.SLDASM, Armario.STL, Caja.sldprt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]
